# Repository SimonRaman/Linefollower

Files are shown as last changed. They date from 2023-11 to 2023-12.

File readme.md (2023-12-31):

# LineFollower

406793047_1077677740050401_2308684094164303501_n

## specifications

microcontroller: Arduino Nano

motors: micro metal gear motoren van Pololu 600 rpm

h-bridge: DRV8833

sensors: QTR-8a

batteries: 2 x 18650 batterijen (samen = 7,2 V)

wireless communication: HC-05

distance sensor - motors: 8 cm

weight: 295 g

speed: 0,61 m/s

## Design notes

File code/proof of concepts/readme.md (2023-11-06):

# Proof of Concepts

Een proof of concept is een combinatie van minimale hard- en software om eenvoudig aan te tonen dat iets werkt.  
Proof of concepts kunnen enerzijds als eerste poging dienen om een bepaald onderdeel van het project werkend te krijgen. Anderzijds kunnen ze tijdens het debuggen van het finale project dienen als test om eventuele hardware problemen te elimineren bij onduidelijke problemen.
<br />  
<br />
Een proof of concept bestaat uit
* een elektronisch schema (indien van toepassing)
* minimale code om de voorop gestelde zaken te demonstreren
* minimale uitleg / aandachtspunten
<br />
De elektronische schakelingen van de proof of concepts komen bij voorkeur overeen met deze van de uiteindelijke linefollower, zodat de code zonder aanpassingen op het finale project kan draaien.

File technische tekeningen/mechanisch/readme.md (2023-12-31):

# mechanische technische tekeningen
In deze map bevinden zich 3 mappen, met name de mappen "LFR1", "LFR2" & "LFR3". De afkorting LFR staat voor "Line Following Robot". Elk van deze mappen bevat een versie van mijn robot waarbij "LFR3" de nieuwste en finale versie is van de LFR. 

## LFR1
Schermafbeelding 2023-12-31 160720

## LFR2
Schermafbeelding 2023-12-31 161631

## LFR3
Schermafbeelding 2023-12-31 160659

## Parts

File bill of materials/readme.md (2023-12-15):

## bill of materials
<br />

|volgnummer|naam|omschrijving|nieuw/recup|kostprijs/stuk|aantal|subtotaal|
|---|----|---|---|---|---|---|
| 1|  Chassis  | Dit is de romp van de auto. | nieuw | € 1 | 1  | € 1 |
| 2|  Spoiler  | Spoiler voor achteraan op de auto. | nieuw | € 1 |  1 | € 1 |
| 3| Schuiver sensor |  Om de afstand van de sensor te regelen. |  nieuw | € 1 | 1  | € 1 |
| 4| Schuiver steunpunt | Om de afstand van het steunpunt te regelen. | nieuw |  € 1 |  1 |  € 1  |
| 5|  Velg  | Vormd samen met een band een wiel. | nieuw | € 1 | 2 | € 1 |
| 6| Playmobile band | Vormd samen met een velg een wiel. | recup | gratis | 2  | gratis |
| 7|  Schakelaar (KCD11-101) | Hoofdschakelaar om de robot in- of uit te schakelen.  | nieuw | € 0,83  | 1 |  € 0,83 |
| 8| DuPont Jumper draad Female-Female 20cm 10 draden | Kabeles om sensor met printplaat te verbinden. | nieuw  | € 0,75 | 2 | € 1,5 |
| 9|  Motorhouder  |  Deze dient om de motor mee te bevestingen aan het chassis | nieuw | € 1  |  1  |  € 1 |
| 10|  Motor  | micro metal gear motor 6V 50:1 | nieuw |  € 3,25 | 2 | € 6,50 |
| 11| Batterij | type batterij: 18650 | recup | € 3,5 | 2 | € 7 |
| 12| 2 x 18650 Batterijhouder | De houder voor de 18650 batterijen | nieuw  | € 1,5 | 1 | € 3 |
| 13|  8 x IR Lijn Tracking Module  | Maakt gebruik van QTR-8A sensoren. | nieuw | € 3,5  | 1 |  € 3,5  |
| 14|  Arduino Nano  | De gebruikte microcontroller | recup | € 2,61 |  1 | € 2,61 |
| 15|  DRV8833  | De gebruikte h-brug  | nieuw | € 0,48 |  1 | € 0,48 |
| 16|  Knop  | De startknop | recup | € 0,1 | 1 |  € 0,1 |
| 17|  5 mm led  | De led die weer geeft of de auto aan- of uit staat  | recup |  € 0,1 |  1 | € 0,1 |
| 18|  Weerstand 220 Ω  | De weerstand voor de led | recup | € 0,05 | 1 | € 0,05 |
| 19|  Weerstand 10 kΩ  |  Pull-down weerstand voor de startknop.  | recup | € 0,05 | 1 | € 0,05 |
| 20|  15 Pins header Female  | / | nieuw | € 0,31	 | 2  | € 0,62 |
| 21|  40 Pins header Male  | / | nieuw | € 0,4 | 1 | € 0,4 |
| 22|  6 Pins header Female  | / | nieuw | € 0,18	 | 3 | € 0,54 |
| 23|  40 Pins header Male - 90 graden  |  /  |  nieuw | € 0,5	  | 1 | € 0,5 |
| 24|  2 Pin Schroef Terminal Block Connector 2.54mm Afstand  | / | nieuw | € 0,30	 | 1 |  € 0,30	 |
| 25|  4 Pin Schroef Terminal Block Connector 2.54mm Afstand  | / | nieuw  | € 0,45 | 1 |  € 0,45 |
| 26|  Bout M3 - 5mm draad - 100 stuks  | / | nieuw  | € 2,5 | 1 | € 2,5 |
| 27|  10 x Afstandsbusje M3 | 6mm bushoogte - 6mm draadhoogte | nieuw  | € 1,5 | 1 | € 1,5 |
| 28|  Printplaat | Hierop wordt alle elektronica bevestigd | nieuw | € 6,71 | 1 | € 6,71 |
| 29| Bluetooth module |  Type: HC-05 | recup | € 3,90 | 1 | € 3,90 |
| 30| Batterij oplader |  / | recup | € 3,69 | 1 | € 3,69 |
| | | | | | Totaal | € 52,33 |

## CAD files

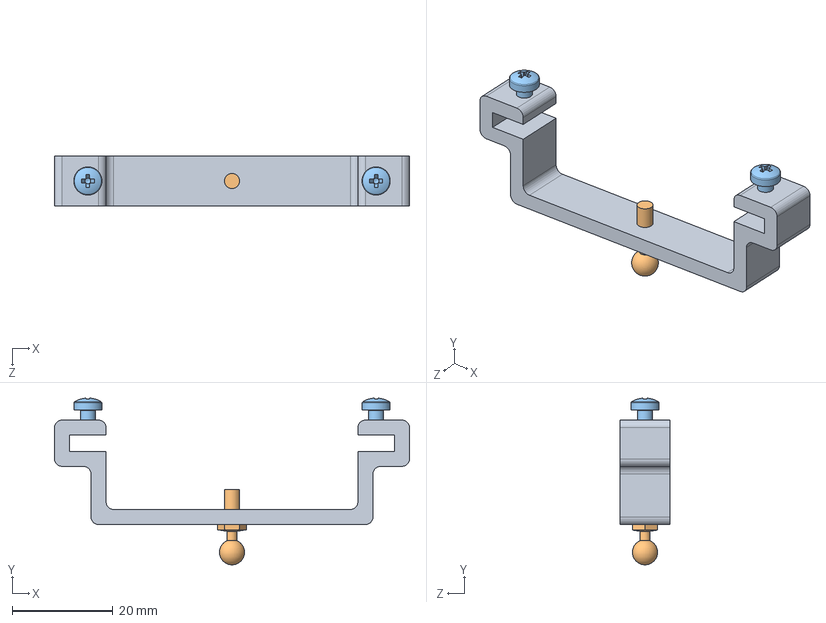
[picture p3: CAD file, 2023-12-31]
technische tekeningen/mechanisch/LFR2/LFR2_Assembly schuiver M3 ronde kop.SLDASM
70.5 x 33.1 x 10.0 mm
M3 ronde kop schuiver
M3 ronde kop
pan head cross recess screw_iso x 2

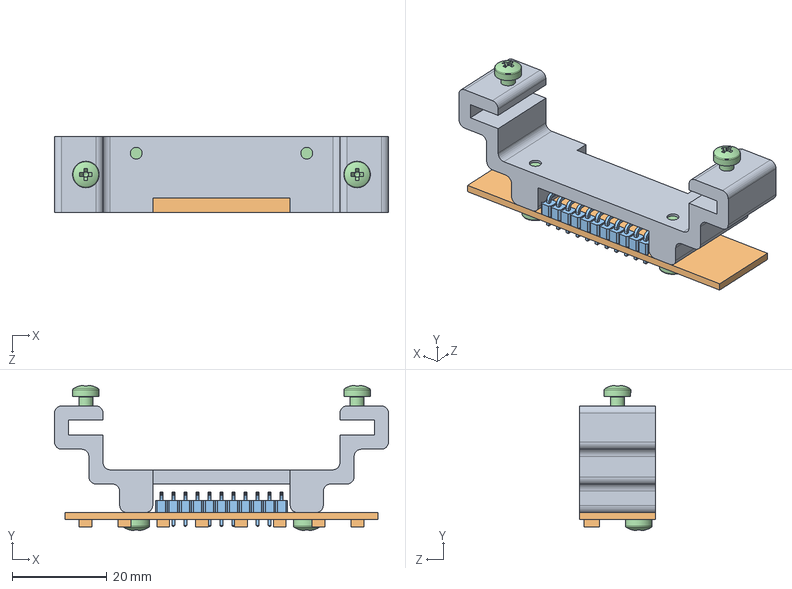
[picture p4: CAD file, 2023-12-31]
technische tekeningen/mechanisch/LFR3/LFR3_Assembly schuiver QTR-8A.SLDASM
70.5 x 30.7 x 16.0 mm
QTR-8A schuiver
QTR-8A
Header11P90
pan head cross recess screw_iso x 4

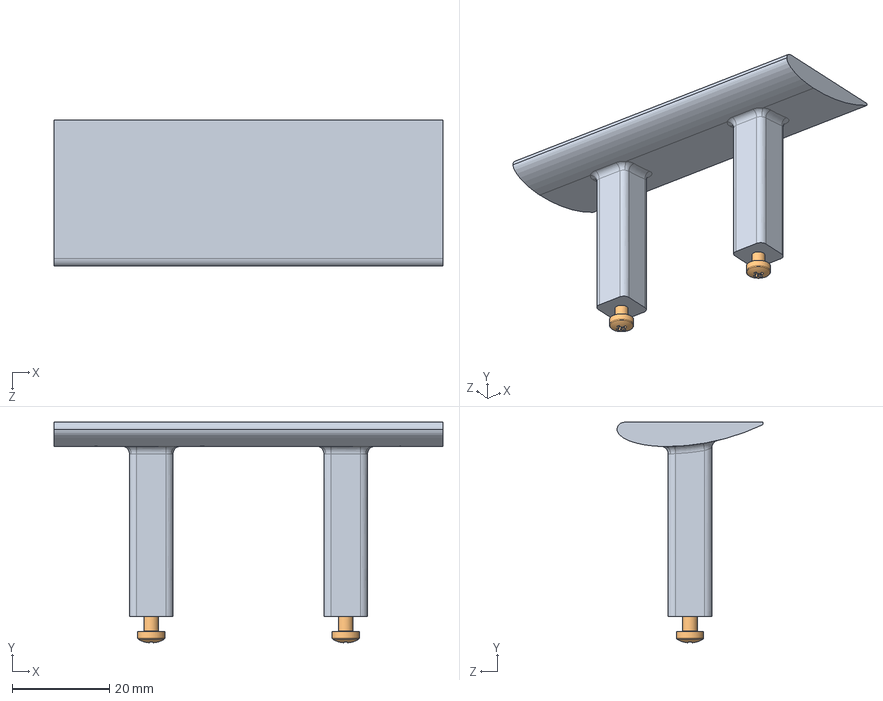
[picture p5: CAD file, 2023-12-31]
technische tekeningen/mechanisch/LFR3/LFR3_Assembly spoiler.SLDASM
80.0 x 45.4 x 30.0 mm
Spoiler
pan head cross recess screw_iso x 2

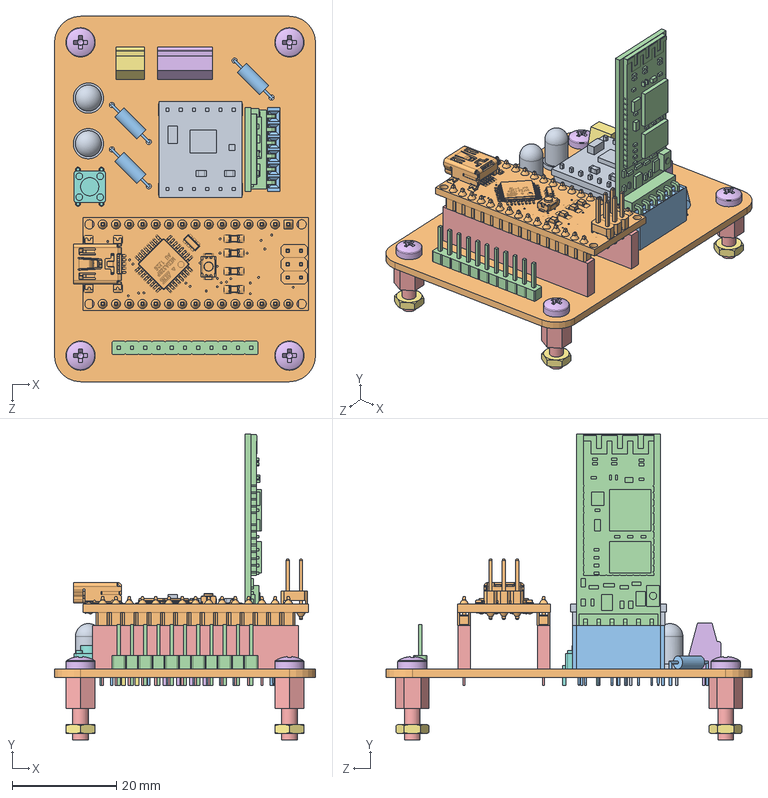
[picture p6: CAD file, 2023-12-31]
technische tekeningen/mechanisch/LFR2/LFR2_Assembly PCB.SLDASM
50.0 x 58.6 x 70.0 mm
DRV8833
Arduino Nano
Header6P x 3
HC-05
Header15P x 2
ScrewTerminal x 4
ScrewTerminal x 2
Push button
Led x 2
PCB 50 x 70
Weerstand x 3
Header11P
M3 spacer 6 mm x 4
pan head cross recess screw_iso x 4
hex thin nut chamfered gradeab_iso x 4

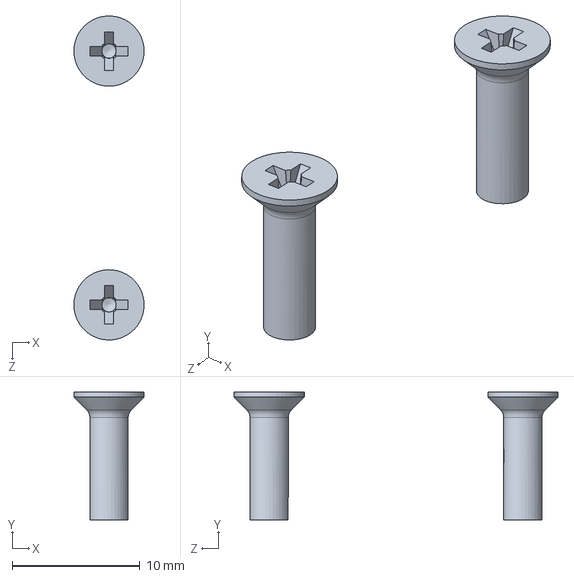
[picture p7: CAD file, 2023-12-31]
technische tekeningen/mechanisch/LFR2/LFR2_Assembly batterijhouder.SLDASM
5.50 x 10.0 x 25.3 mm
countersunk flat head cross recess screw_iso x 2

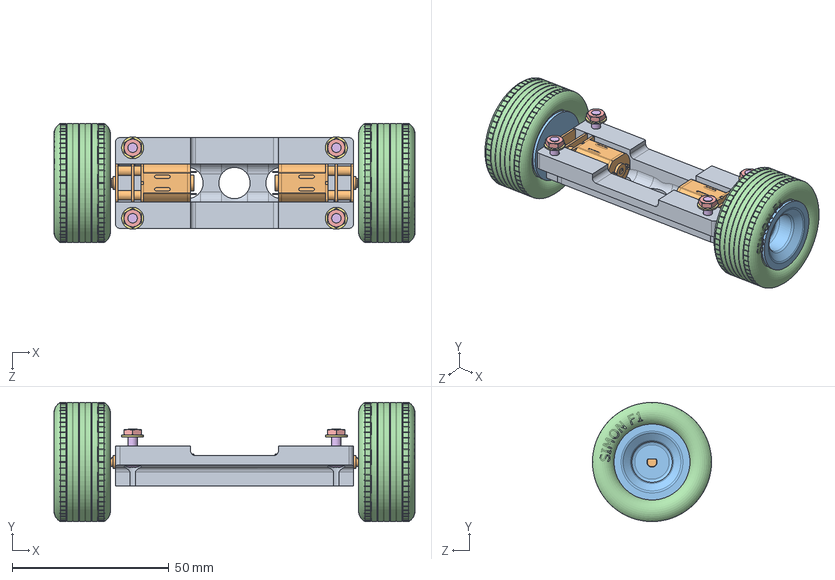
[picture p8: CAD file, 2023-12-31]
technische tekeningen/mechanisch/LFR3/LFR3_Assembly wiel.SLDASM
115.2 x 38.0 x 38.0 mm
Motor mount
Micro Metal Gear Motor x 2
Velg x 2
Band x 2
hex thin nut chamfered gradeab_iso x 4
pan head cross recess screw_iso x 4
plain washer normal grade a_iso x 4

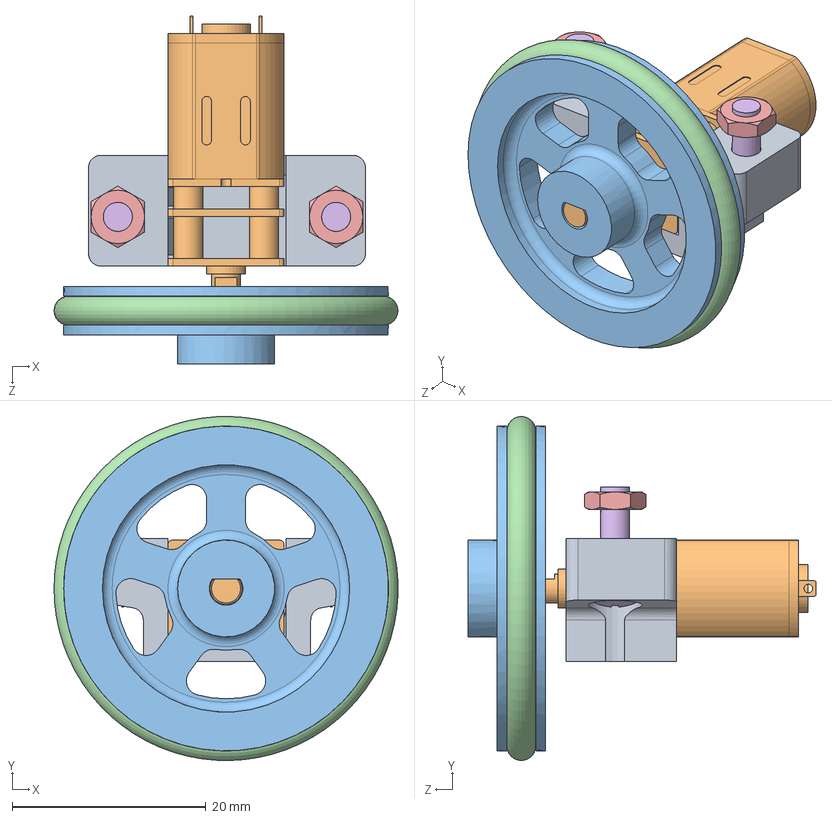
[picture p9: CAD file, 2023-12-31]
technische tekeningen/mechanisch/LFR2/LFR2_Assembly wiel.SLDASM
35.5 x 35.5 x 35.9 mm
Motor mount
Micro Metal Gear Motor
Wiel 29.5 x 3
O-ring 29.5 x 3
hex thin nut chamfered gradeab_iso x 2
pan head cross recess screw_iso x 2

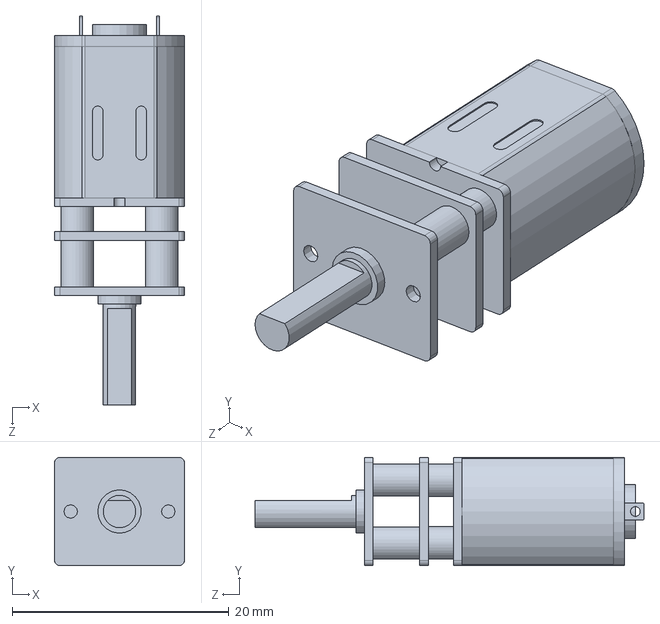
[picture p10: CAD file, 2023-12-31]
technische tekeningen/mechanisch/LFR1/LFR1_Micro Metal Gear Motor.SLDPRT
12.0 x 10.0 x 35.9 mm

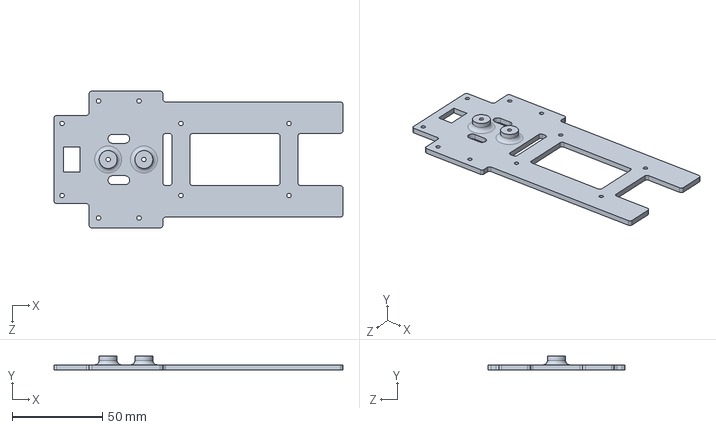
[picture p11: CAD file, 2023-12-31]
technische tekeningen/mechanisch/LFR3/LFR3_Chassis.SLDPRT
160.5 x 8.00 x 76.0 mm

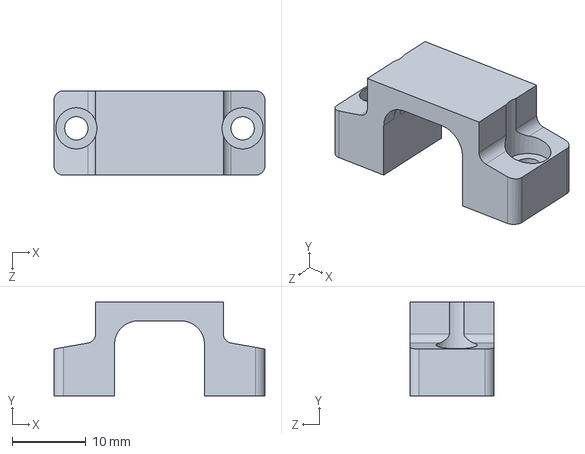
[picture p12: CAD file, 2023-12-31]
technische tekeningen/mechanisch/LFR2/LFR2_Motor mount.sldprt
28.6 x 12.7 x 11.4 mm

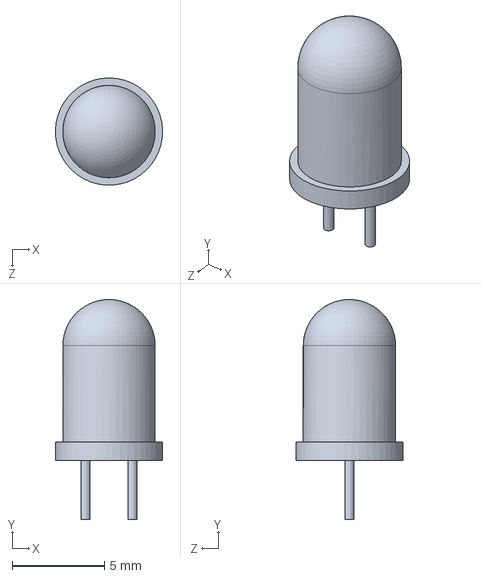
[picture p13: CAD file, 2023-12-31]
technische tekeningen/mechanisch/LFR1/LFR1_Led.SLDPRT
5.80 x 11.9 x 5.79 mm

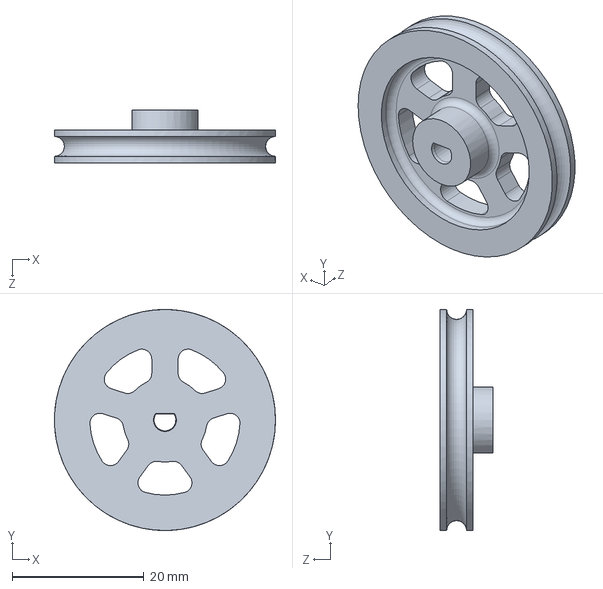
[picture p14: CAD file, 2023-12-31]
technische tekeningen/mechanisch/LFR2/LFR2_Wiel 29.5 x 3.SLDPRT
33.5 x 33.5 x 8.00 mm

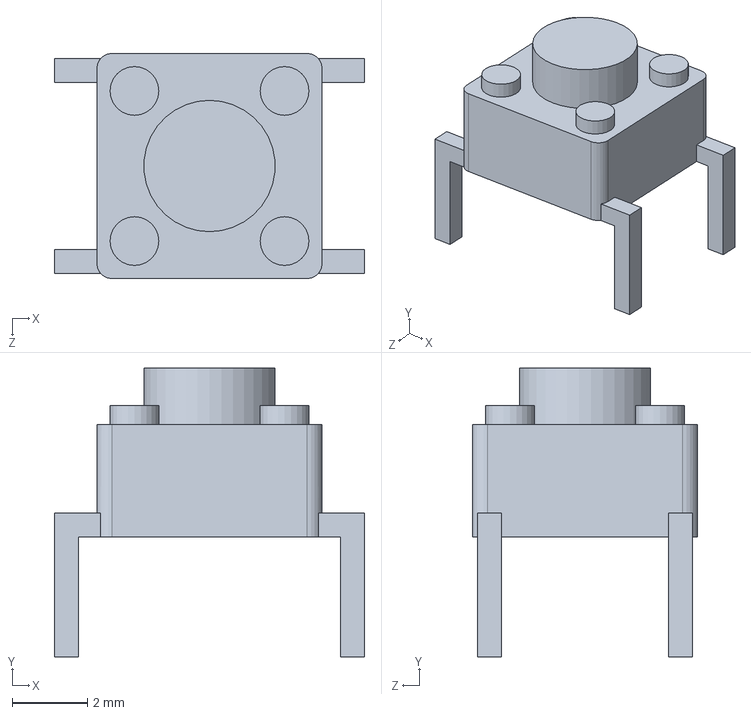
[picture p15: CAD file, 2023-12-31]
technische tekeningen/mechanisch/LFR1/LFR1_Push button.SLDPRT
8.26 x 7.70 x 6.00 mm

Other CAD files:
technische tekeningen/mechanisch/LFR3/LFR3_Assembly schuiver M3 ronde kop.SLDASM
technische tekeningen/mechanisch/LFR2/LFR2_Assembly spoiler.SLDASM
technische tekeningen/mechanisch/LFR3/LFR3_Assembly batterijhouder.SLDASM
technische tekeningen/mechanisch/LFR2/LFR2_Assembly schuiver QTR-8A.SLDASM
technische tekeningen/mechanisch/LFR3/LFR3_Assembly PCB.SLDASM
technische tekeningen/mechanisch/LFR1/LFR1_Base.SLDPRT
technische tekeningen/mechanisch/LFR1/LFR1_M3 Ronde Kop.SLDPRT
technische tekeningen/mechanisch/LFR1/LFR1_Micro Metal Gear Motor Bracket.SLDPRT
technische tekeningen/mechanisch/LFR1/LFR1_PCB 50 x 70.SLDPRT
technische tekeningen/mechanisch/LFR1/LFR1_QTR-8A plaatje.SLDPRT
technische tekeningen/mechanisch/LFR1/LFR1_QTR-8A.SLDPRT
technische tekeningen/mechanisch/LFR1/LFR1_ScrewTerminal x 2.SLDPRT
technische tekeningen/mechanisch/LFR1/LFR1_ScrewTerminal x 4.SLDPRT
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

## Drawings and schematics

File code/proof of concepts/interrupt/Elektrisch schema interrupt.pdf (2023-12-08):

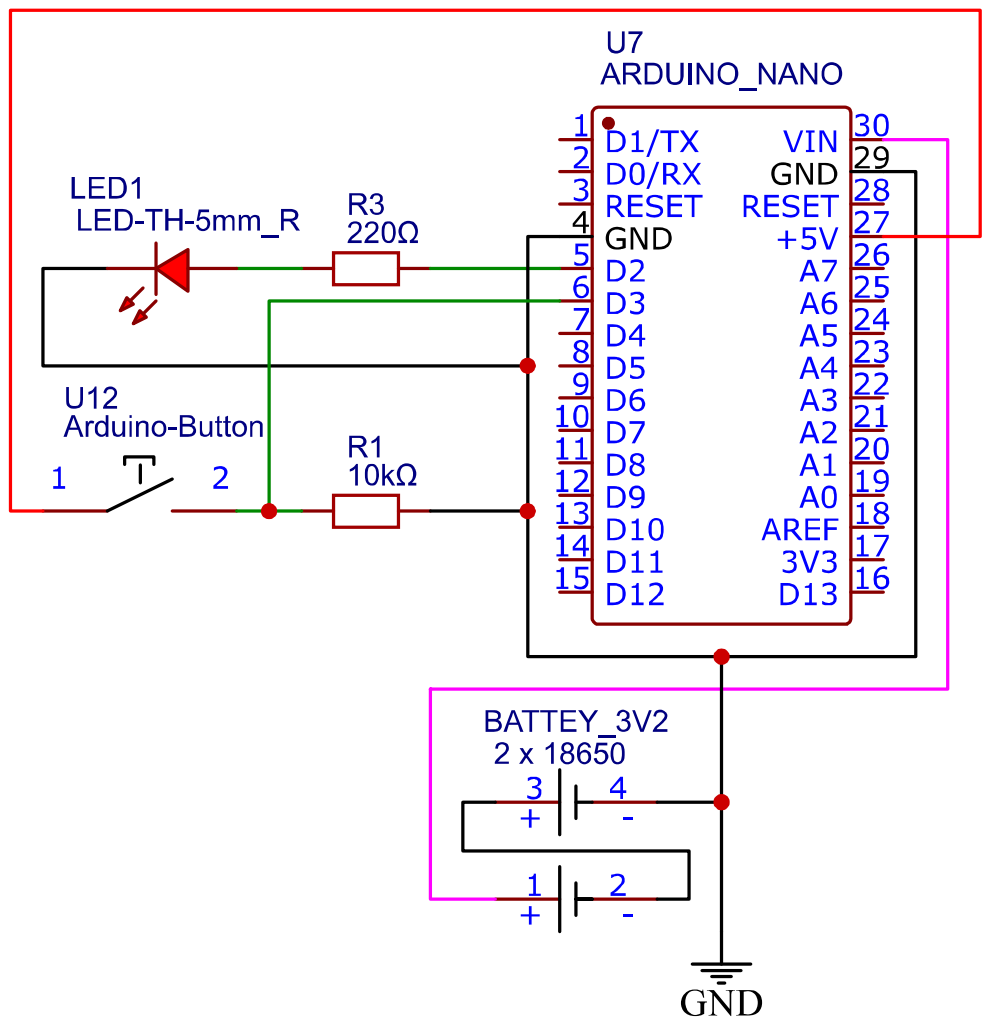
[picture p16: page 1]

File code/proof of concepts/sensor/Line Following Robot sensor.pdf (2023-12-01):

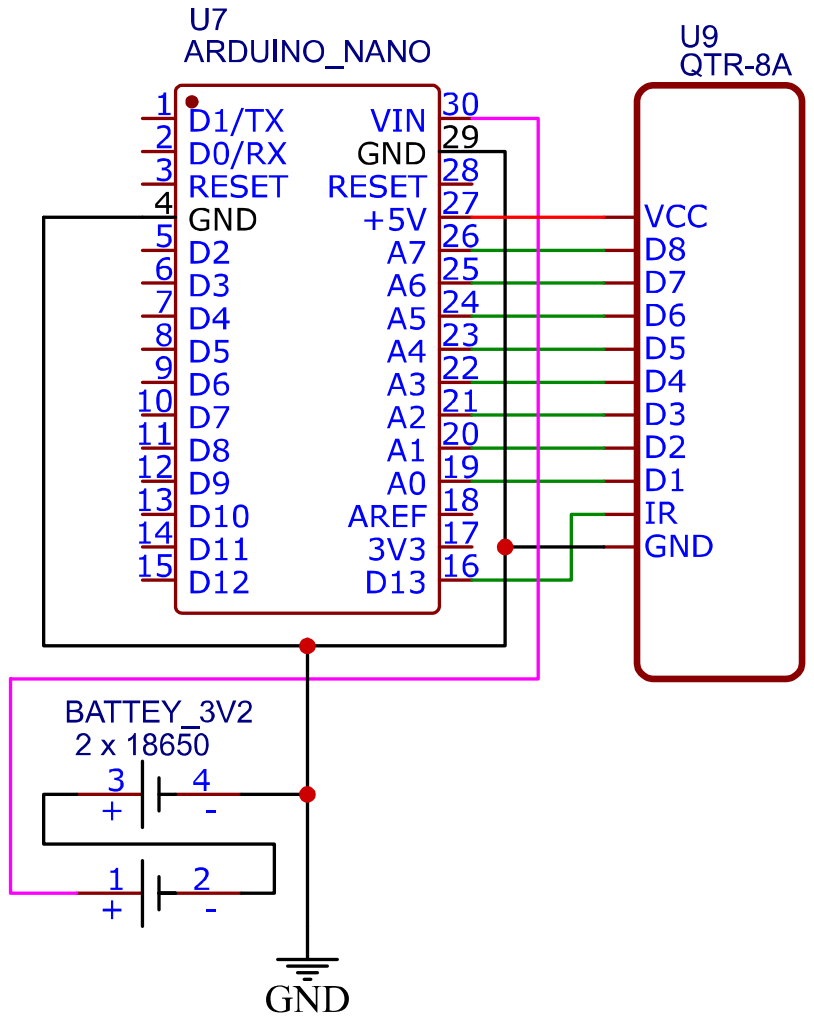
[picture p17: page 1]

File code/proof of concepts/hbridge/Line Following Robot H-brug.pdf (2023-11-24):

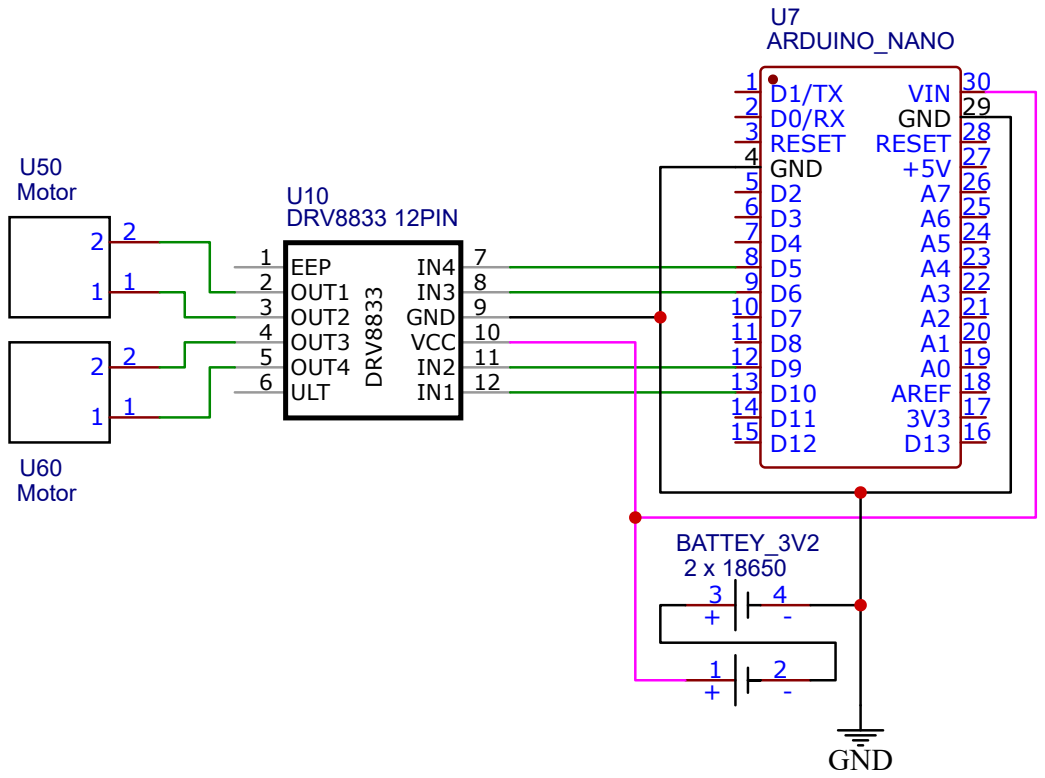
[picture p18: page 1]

Drawn By: Simon Raman

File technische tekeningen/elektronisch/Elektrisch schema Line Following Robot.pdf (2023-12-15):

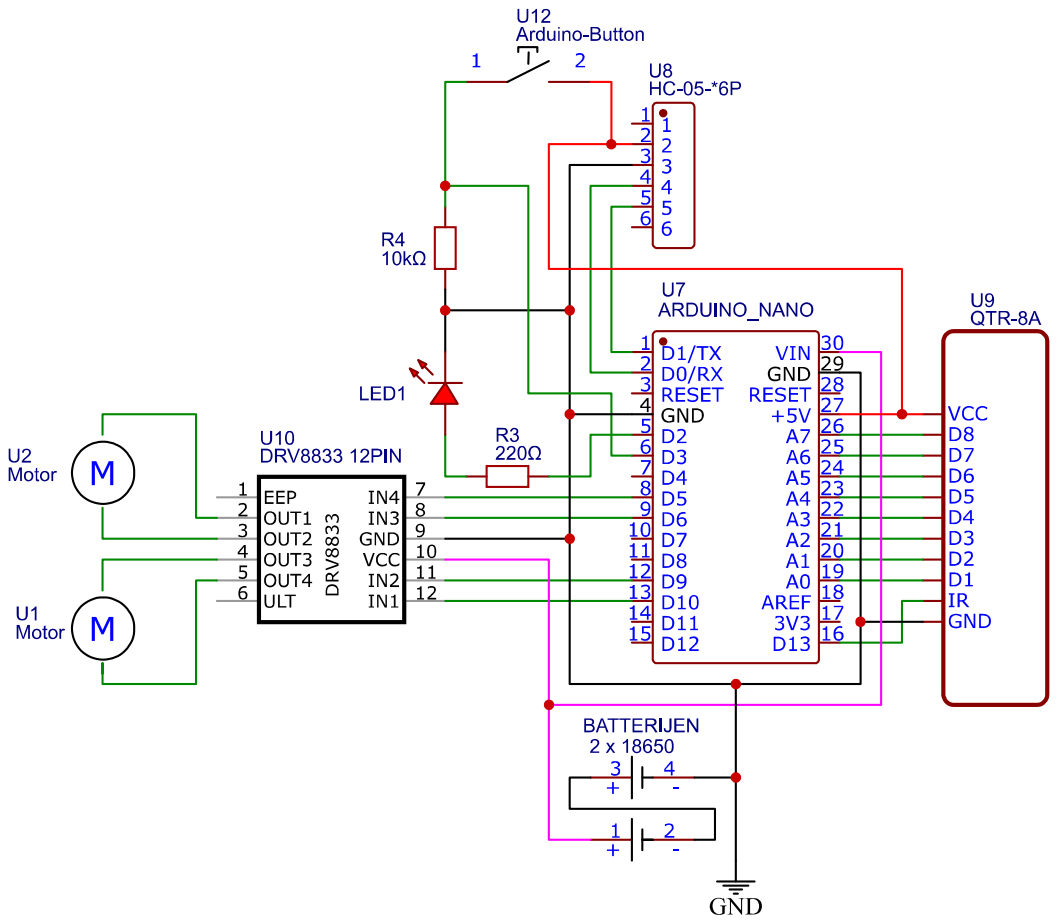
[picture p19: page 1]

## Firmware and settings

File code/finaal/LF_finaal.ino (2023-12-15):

#include "SerialCommand.h"
#include "EEPROMAnything.h"

#define SerialPort Serial
#define Baudrate 9600

#define MotorLeftForward 6
#define MotorLeftBackward 5
#define MotorRightForward 10
#define MotorRightBackward 9


const int Drukknop = 3;//interupt
const int LED = 2; //Led
const int IR = 13; //SensorLED

//interupt:
volatile bool runState = false;
volatile unsigned long lastDebounceTime = 0;  // Tijd voor debouncing
unsigned long debounceDelay = 50;  // Debounce-tijd in milliseconden


SerialCommand sCmd(SerialPort);
bool debug;
bool run;                   
unsigned long previous, calculationTime;


const int sensor[] = {A7, A6, A5, A4, A3, A2, A1, A0};


struct param_t
{
  unsigned long cycleTime;
  int black[8];
  int white[8];
  float diff;
  float kp;
  int power;
  float ki;
  float kd;

} params;

int normalised[8];
float debugposition;
float output;
float error;
float iTerm = 0;
float lastErr;


void setup()
{
  pinMode(10, OUTPUT);
  pinMode(9, OUTPUT);
  pinMode(6, OUTPUT);
  pinMode(5, OUTPUT);

  SerialPort.begin(Baudrate);

  sCmd.addCommand("set", onSet);
  sCmd.addCommand("debug", onDebug);
  sCmd.addCommand("calibrate", onCalibrate);
  sCmd.addCommand("run", onRun);
  sCmd.addCommand("stop", onStop);
  sCmd.setDefaultHandler(onUnknownCommand);

  EEPROM_readAnything(0, params);
  SerialPort.println("ready");

  //Interupt
  pinMode(Drukknop, INPUT);
  attachInterrupt(digitalPinToInterrupt(Drukknop), Interrupt, RISING);

  pinMode(LED, OUTPUT);

  pinMode(IR, OUTPUT);
  digitalWrite(IR, HIGH);
}


void loop()
{
  sCmd.readSerial();
 
  unsigned long current = micros();
  if (current - previous >= params.cycleTime)
  {
    previous = current;
    //normalize
    for (int i = 0; i < 8; i++)
    {
      normalised[i] = map(analogRead(sensor[i]), params.black[i], params.white[i], 0, 1000);
      
    }

    //interpolatie
    int index = 0;
    float position;

    for (int i = 1; i < 8; i++) if (normalised[i] < normalised[index]) index = i;

    if (normalised[index] > 1200) run = false;
    

    if (index == 0) position = -30;
    else if (index == 7) position = 30;
    else
    {
      int sNul = normalised[index];
      int sMinEen = normalised[index-1];
      int sPlusEen = normalised[index+1];

      float b = sPlusEen - sMinEen;
      b = b / 2;

      float a = sPlusEen - b - sNul;

      position = -b / (2 * a);
      position += index;
      position -= 3.5;

      position *= 9.525; //afstand sensoren uit elkaar waarschijnlijk aanpassen

    }
    
    debugposition = position;
    
    //P-regelaar
    error = -position;
    output = error * params.kp;

    //I-Regelaar
    iTerm += params.ki * error;
    iTerm = constrain(iTerm, -510, 510);
    output += iTerm;

    //D-Regelaar
    output += params.kd * (error - lastErr);
    lastErr = error;

    output = constrain(output, -510, 510);

    int powerLeft = 0;
    int powerRight = 0;


    if (run) if (output >= 0)
    {
      powerLeft = constrain(params.power + params.diff * output, -255, 255);
      powerRight = constrain(powerLeft - output, -255, 255);
      powerLeft = powerRight + output;
    }
    else
    {
      powerRight = constrain(params.power - params.diff * output, -255, 255);
      powerLeft = constrain(powerRight + output, -255, 255);
      powerRight = powerLeft - output;
        
    }

    analogWrite(MotorLeftForward, powerLeft > 0 ? powerLeft : 0);
    analogWrite(MotorLeftBackward, powerLeft < 0 ? -powerLeft : 0);
    analogWrite(MotorRightForward, powerRight > 0 ? powerRight : 0);
    analogWrite(MotorRightBackward, powerRight < 0 ? -powerRight : 0);
  }
  
  unsigned long difference = micros() - current;
  if (difference > calculationTime) calculationTime = difference;

}

void onUnknownCommand(char *command)
{
  SerialPort.print("unknown command: \"");
  SerialPort.print(command);
  SerialPort.println("\"");
}


void onSet()
{
  char* param = sCmd.next();
  char* value = sCmd.next();  
  
  if (strcmp(param, "cycle") == 0)
  {
    long newCycleTime = atol(value);
    float ratio = ((float) newCycleTime) / ((float) params.cycleTime);

    params.ki *= ratio;
    params.kd /= ratio;

    params.cycleTime = newCycleTime;
  }

  else if (strcmp(param, "ki") == 0)
  {
    float cycleTimeInSec = ((float) params.cycleTime) / 1000000;
    params.ki = atof(value) * cycleTimeInSec;
  }

  else if (strcmp(param, "kd") == 0)
  {
    float cycleTimeInSec = ((float) params.cycleTime) / 1000000;
    params.kd = atof(value) / cycleTimeInSec;
  }

  else if (strcmp(param, "power") == 0) params.power = atol(value);
  else if (strcmp(param, "diff") == 0) params.diff = atof(value);
  else if (strcmp(param, "kp") == 0) params.kp = atof(value);

  EEPROM_writeAnything(0, params);
}

void onDebug()
{
  SerialPort.print("cycle time: ");
  SerialPort.println(params.cycleTime);
  
  /* parameters weergeven met behulp van het debug commando doe je hier ... */
  SerialPort.print("black: ");
  for (int i = 0; i < 8; i++)
  {
    SerialPort.print(params.black[i]);
    SerialPort.print(" ");
  }
  SerialPort.println(" ");

  SerialPort.print("white: ");
  for (int i = 0; i < 8; i++)
  {
    SerialPort.print(params.white[i]);
    SerialPort.print(" ");
  }
  SerialPort.println(" ");

  SerialPort.print("Normalised: ");
  for (int i = 0; i < 8; i++)
  {
    SerialPort.print(normalised[i]);
    SerialPort.print(" ");
  }
  SerialPort.println(" ");

  SerialPort.print("position: ");
  SerialPort.println(debugposition);

  SerialPort.print("Power: ");
  SerialPort.println(params.power);

  SerialPort.print("diff: ");
  SerialPort.println(params.diff);

  SerialPort.print("kp: ");
  SerialPort.println(params.kp);

  float cycleTimeInSec = ((float) params.cycleTime) / 1000000;
  float ki = params.ki / cycleTimeInSec;
  SerialPort.print("Ki: ");
  SerialPort.println(ki);

  float kd = params.kd * cycleTimeInSec;
  SerialPort.print("Kd: ");
  SerialPort.println(kd);

  SerialPort.print("RUN: ");
  SerialPort.println(params.kp);
  
  SerialPort.println(" ");
  SerialPort.print("calculation time: ");
  SerialPort.println(calculationTime);
  calculationTime = 0;
}

void onCalibrate()
{
  char* param = sCmd.next();

  if (strcmp(param, "black") == 0)
  {
    SerialPort.print("start calibrating black...");
    for (int i = 0; i < 8; i++) params.black[i] = analogRead(sensor[i]);
    SerialPort.println("done");
  }
  else if (strcmp(param, "white") == 0)
  {
    SerialPort.print("start calibrating white...");
    for (int i =0; i < 8; i++) params.white[i] = analogRead(sensor[i]);
    SerialPort.println("done");
  }

  EEPROM_writeAnything(0, params);
}

void onRun()
{
  run = true;
  digitalWrite(LED, HIGH);
}

void onStop()
{
  run = false;
  digitalWrite(LED, LOW);
}

void Interrupt()
{
  // Lees de status van de drukknop
  int buttonState = digitalRead(Drukknop);

  // Debounce de drukknop met millis
  if ((millis() - lastDebounceTime) > debounceDelay) {
    // Als de knop opgaand is, wissel de status van de LED
    if (buttonState == HIGH) {
      runState = !runState;

      // Schakel de LED in of uit op basis van de nieuwe status
      digitalWrite(LED, runState);
      run = runState;
      iTerm = 0;
    }

    // Update de tijd van de laatste debouncing
    lastDebounceTime = millis();
  }
  
}

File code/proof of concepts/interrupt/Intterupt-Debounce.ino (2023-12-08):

const int buttonPin = 3;   // Druknop op pin 12
const int ledPin = 2;      // LED op pin 2

volatile bool ledState = false;  // Huidige status van de LED
volatile unsigned long lastDebounceTime = 0;  // Tijd voor debouncing
unsigned long debounceDelay = 50;  // Debounce-tijd in milliseconden

void setup() 
{
  pinMode(buttonPin, INPUT);  // Configureer pin 2 als ingang met pull-up weerstand
  pinMode(ledPin, OUTPUT);           // Configureer pin 3 als uitgang

  attachInterrupt(digitalPinToInterrupt(buttonPin), buttonInterrupt, RISING);  // Koppel de interrupt-functie aan de opgaande flank van de drukknop
}

void loop() 
{
  // Doe hier andere taken die onafhankelijk zijn van de drukknopstatus
}

void buttonInterrupt() {
  // Lees de status van de drukknop
  int buttonState = digitalRead(buttonPin);

  // Debounce de drukknop met millis
  if ((millis() - lastDebounceTime) > debounceDelay) 
  {
    // Als de knop opgaand is, wissel de status van de LED
    if (buttonState == HIGH) 
    {
      ledState = !ledState;

      // Schakel de LED in of uit op basis van de nieuwe status
      digitalWrite(ledPin, ledState);
    }

    // Update de tijd van de laatste debouncing
    lastDebounceTime = millis();
  }
}
